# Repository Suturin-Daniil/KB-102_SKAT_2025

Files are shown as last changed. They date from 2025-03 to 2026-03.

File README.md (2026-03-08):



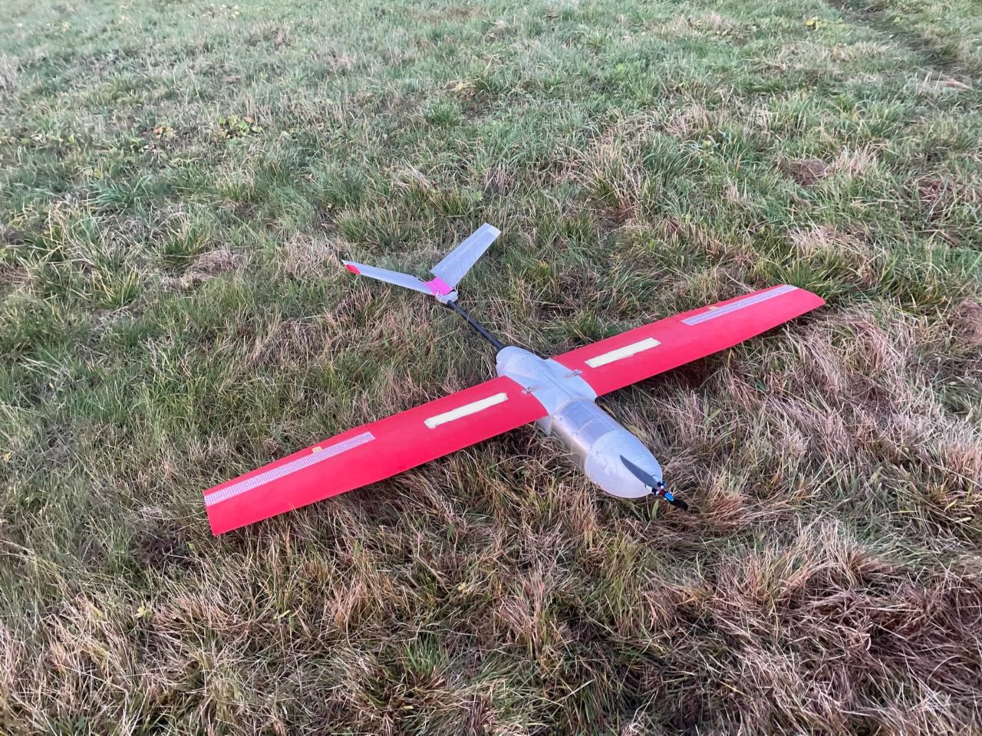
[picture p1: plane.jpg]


# Репозиторий команды КБ-102

В этом репозитории содержится процесс разработки ЛА командой "КБ-102" в рамках студенческого конкурса авиамодельного творчества СКАТ 2025

## Структура репозитория

- **КонцептуальныйДизайн** - папка содержит резльтаты концептуального дизайна ЛА. Описание аэродинамической схемы. Начальная модель ЛА

<!-- - **ПромежуточныйДизайн** - папка промежуточного отчета, содержащая детализированую модель ЛА, начальные аэродинамические и прочностные исследования. Описано бортовое оборудование

- **Изготовление** - папка производственного отчета, содержит конечный вариант детальной модели ЛА, представлены результаты численного моделирования полета ЛА, статической и динамической стабильности. Прочностные расчеты

- **ПолетныйКонтроллер** - содержит электрические схемы полетного контроллера и платы распределения питания собственной разработки. А также динамическую модель ЛА и разрабатываемый автопилот-->

- **Смета** - смета на полетный контроллер и ЛА 

График работ (https://disk.yandex.ru/i/gJ8DDl-IPzN4OA)

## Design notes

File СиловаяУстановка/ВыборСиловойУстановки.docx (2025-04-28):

# 1 Силовая установка

# 1.1 Выбор воздушного винта

Подход к выбору формы и размера пропеллера основан на экспериментальных данных, полученных при испытании воздушных винтов в аэродинамической трубе [1]. Команда выбирала пропеллеры, которые бы давали необходимую тягу для выбранной скорости горизонтального полета с диапазоном частот вращения, который включен в набор угловых скоростей вращения в экспериментальных данных ( 3000÷6000 мин^(-1) ) [1], чтобы быть уверенными в полученных командой оценках. Согласно теории [2 стр. 52], разработанной для оценки тяги и механического момента винта, их выражения имеют следующий вид:

| T= (ρD^4)/(4π^2)Ω^2 C_T | (1)
| Q_p = (ρD^5)/(4π^2)Ω^2 C_Q | (2)

Безразмерные коэффициенты тяги и момента винта могут быть разложены в ряд по степеням поступи винта J= (2πV_a)/(ΩD) (3-4). На рисунке 1 представлены графики зависимости коэффициентов винта от поступи и линии квадратичной аппроксимации.

| C_T =C_(T_0) +C_(T_1) J+C_(T_2) J^2 | (3)
| C_Q =C_(Q_0) +C_(Q_1) J+C_(Q_2) J^2 | (4)

Для оценки потребной тяги при горизонтальном полете со скоростью 18 м/с воспользуемся формулой согласно [3 стр. ]:

| T= W/K= 35/10=3.5 Н | (5)

В ходе анализа различных воздушных винтов, удовлетворяющих требованиям потребной тяги, был выбран винт AeroNaut 11x8

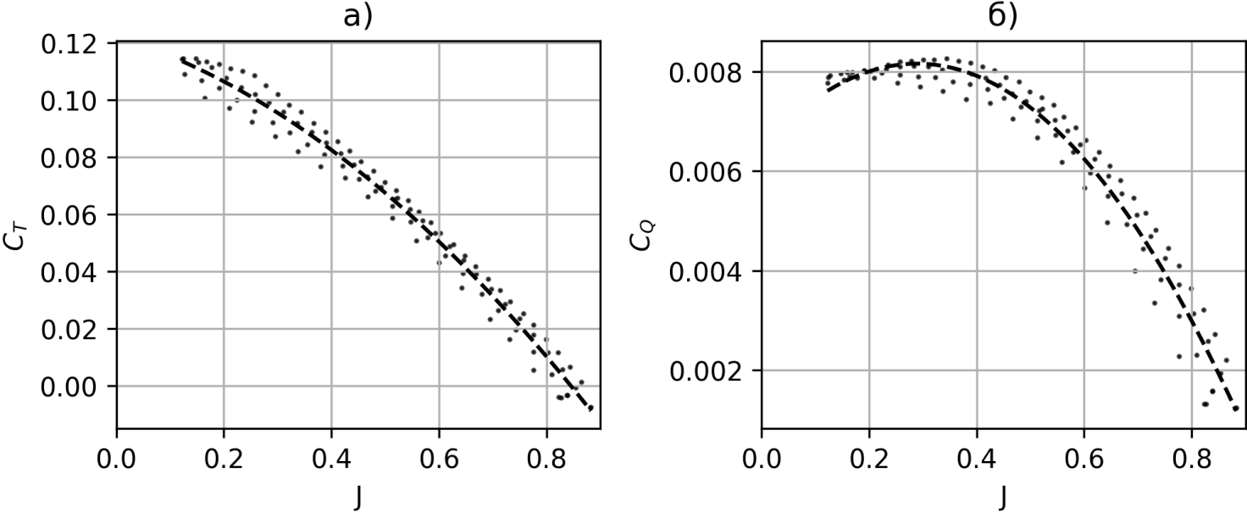
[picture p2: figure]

Рисунок 1 – Коэффициент тяги а) и момента б) винта AeroNaut 11x8

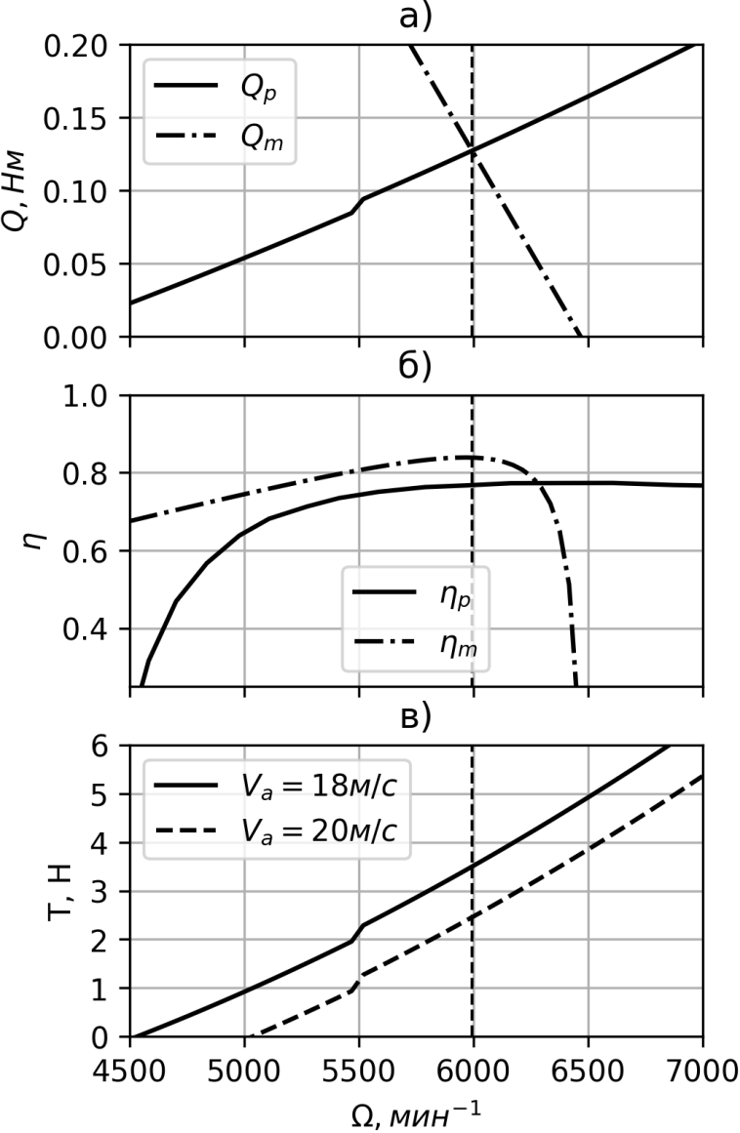
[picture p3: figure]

Рисунок 2 – Выбор оптимальных параметров мотора X2814 и винта AeroNaut 11x8 при горизонтальном полете V_a =18 м/с . а) – пересечение кривых моментов винта и мотора. б) – кривые эффективности мотора и винта. в) – кривые тяги винта. Вертикальная пунктирная линия указывает рабочую частоту вращения

# 1.2 Выбор мотора

В ходе анализа ряда моторов (таблица 1) был выбран Sunnysky X2814 900 kv, так как он оптимален по потребляемой мощности для всех рассматриваемых воздушных винтов. Согласно [2 стр. 53] из равенства механических моментов винта и мотора была найдена точка пересечения кривых моментов винта и мотора (рисунок 2а), соответствующая угловой скорости вращения 6000 мин⁻¹.

Q_m =K_Q (((V_(in) -K_V Ω))/(R-i_0))=Q_p | (6)

Также были построены кривые КПД мотора и винта на рисунке 2б, чтобы убедиться в оптимальном режиме работы ВМГ в выбранном диапазоне угловых частот вращения. Как видно на рисунке 2б, и мотор, и винт на частоте 6000 мин⁻¹ имеет КПД близкий к максимальному для выбранной скорости воздушного полета V_a =18 м/с , η_p = 0.78, η_m =0.84

На рисунке 3в представлены кривые тяги винта в зависимости от частоты вращения для двух разных скоростей воздушного потока. При выбранной скорости 17 м/с винт создает достаточную тягу T=3.5 Н для поддержания установившегося горизонтального полета.

Согласно выражению (6) и рисунку 2а можем оценить мощность, потребляемую ВМГ, с учетом эффективности регулятора оборотов η_(ESC) ≈0.85 :

P=(((Q_m)/(K_V +i_0)))/(η_(ESC))V_(in) ≈110 ВТ | (7)

# 1.3 Оценка энергопотребления

Оценим энергопотребление СУ и БО, согласно расчетам потребления мотора, приведенным выше, и данным о потребляемой мощности для ПК, датчиков, сервоприводов. Ниже в таблице 1 представлены мощности отдельных элементов БО и СУ.

ВМГ | ПК, датчики, связь | Сервоприводы
110 Вт | 7 Вт | 10 Вт

Таблица 1 – энергопотребление элементов бортового оборудования и СУ

Винт Мотор | APC 11x7E¹ (6200 RPM) | APC 11x7S² (5800 RPM) | APC 12x6E¹ (6400 RPM) | AeroNaut 11x8F³ (5800 RPM) | APC 11x8E¹ (5800 RPM) | AeroNaut 12x8F³ (5600 RPM)
T-Motor AT2814 900 kv | 98 Вт | 105 Вт | 105 Вт | 96 Вт | 102 Вт | 107 Вт
T-Motor AT2820 880 kv | 100 Вт | 100 Вт | 101 Вт | 92 Вт | 97 Вт | 101 Вт
T-Motor AT2814 1050 kv | 99 Вт | 99 Вт | 100 Вт | 91 Вт | 96 Вт | 101 Вт
T-Motor AT2820 1050 kv | 101 Вт | 100 Вт | 102 Вт | 93 Вт | 98 Вт | 102 Вт
Sunnysky X2814 900 kv | 96 Вт | 101 Вт | 105 Вт | 94 Вт | 93 Вт | 97 Вт
Sunnysky X2814 1000 kv | 98 Вт | 103 Вт | 106 Вт | 95 Вт | 95 Вт | 99 Вт
Sunnysky X2820 800 kv | 95 Вт | 100 Вт | 103 Вт | 92 Вт | 92 Вт | 96 Вт
Sunnysky X2820 920 kv | 95 Вт | 99 Вт | 103 Вт | 92 Вт | 92 Вт | 96 Вт

Таблица 2 – Энергопотребление моторов при вращении различных воздушных винтов при скорости набегающего потока воздуха 18 м/с и тяге T=3.5 H ¹ Thin Electric, ² Sport, ³ Складной винт

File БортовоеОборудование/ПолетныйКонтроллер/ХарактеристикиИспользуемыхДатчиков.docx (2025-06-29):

Характеристики используемого бортового оборудования и полетного контроллера

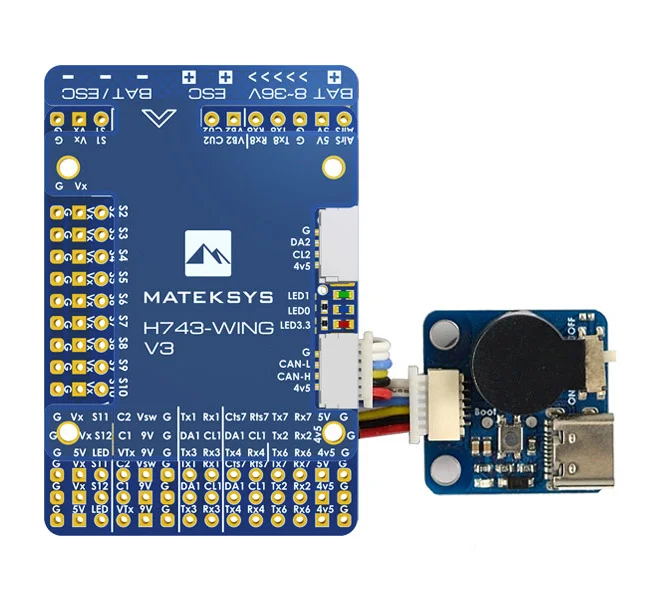
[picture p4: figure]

1. Полётный контроллер MATEKSYS H743-WING V3

Параметр | Значение
Микроконтроллер | STM32H743VIT6 (480 МГц)
Интерфейсы | UART (7) PWM (13) I2C (2) CAN (1)
Прошивка | ArduPilot
Входное напряжение | 8 - 36 В (3-8S LiPo)
Потребляемый ток | 160 мА
Размеры | 54мм × 36мм × 13мм
Вес | 30 г
Стоимость | 13700р (https://mydrone.ru/poletnyy-kontroller-mateksys-h743-wing-v3/)

2. Приемник (телекоманды) Mateksys ELRS 2,4 ГГц

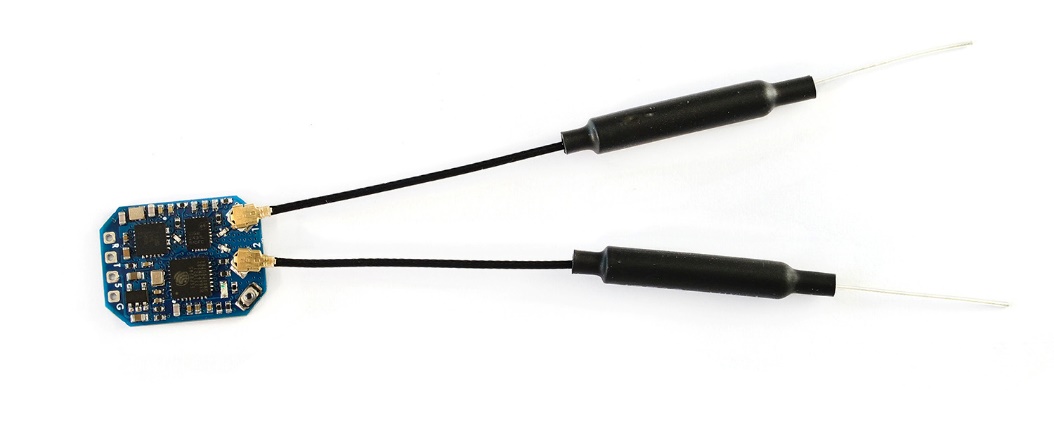
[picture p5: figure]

Параметр | Значение
Антенный разъем | IPEX MHF 1
Рабочая частота | 2,4 ГГц (2400–2480 МГц)
Мощность передачи | 22,5–23 дБм
Коэффициент усиления RX | 12,5 дБ
Протокол приемника | CRSF
Входное напряжение | 4–9 В (контакт 5 В)
Потребляемый ток | 40–45 мА (до привязки) 70–75 мА (привязка)
Размеры | 21мм × 15мм × 5мм
Вес | 3 г
Стоимость | 1800р (https://aliexpress.ru/item/1005006832122747.html?sku_id=12000038446411131)

3. ГНСС и компас Mateksys M10Q-5883

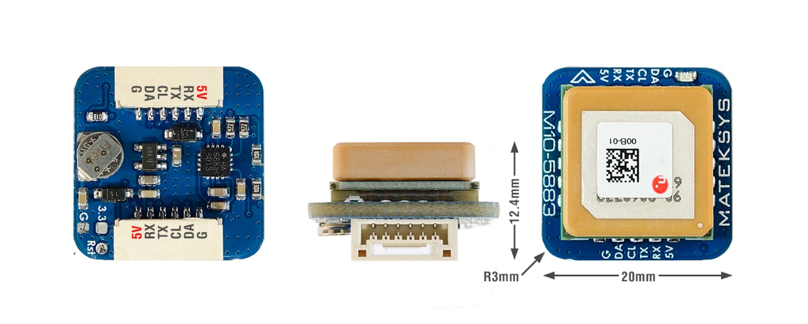
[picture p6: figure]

Параметр | Значение
Патч-антенна | 15 × 15 × 4 мм
Диапазон входного напряжения | 4–9 В (контакт 5 В)
Потребляемый ток | 13 мА
Скорость передачи UART | 9600 (по умолчанию)
Рабочие температуры | -20–80 °C
Интерфейсы | UART (TX, RX) для GNSS I2C (DA, CL) для компаса QMC5883L
Разъем | JST-GH-6P (SM06B-GHS-TB), шаг 1,27 мм
Размеры | 20мм × 20мм × 12,4 мм
Вес | 8 г
Стоимость | 4540р (https://amperkot.ru/msk/catalog/navigatsionnyiy_modul_s_kompasom_mateksys_gnss_m105883-40002749.html)

4. Цифровой датчик воздушной скорости Mateksys ASPD-4525

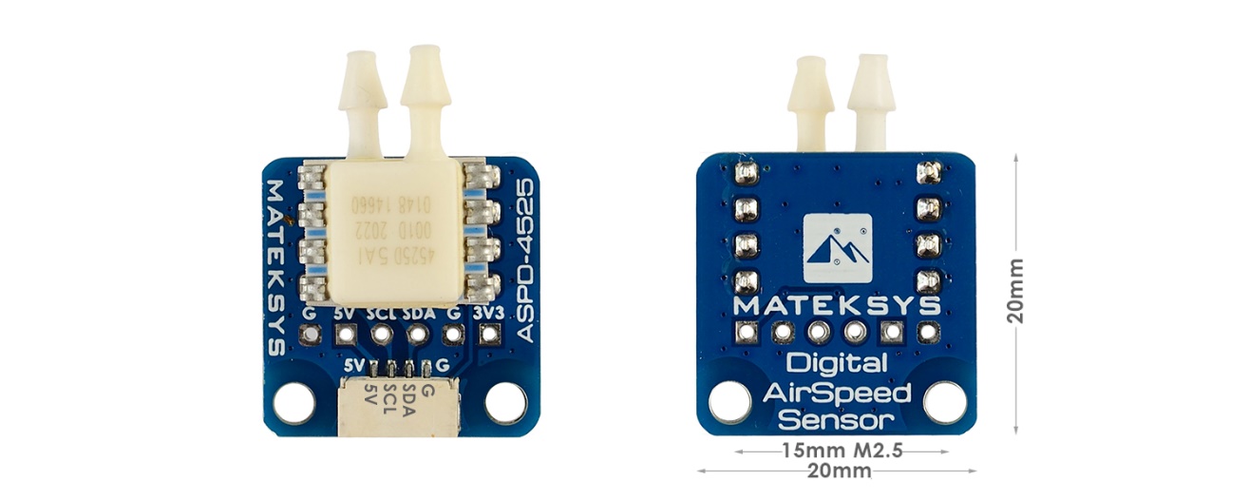
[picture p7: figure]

Параметр | Значение
Напряжение питания платы | 4–5 В
Датчик | TE 4525DO-DS5AI001DP
Потребляемый ток | 5 мА
Интерфейс | I2C (SCL и SDA)
Диапазоны давления | 1 psi (0,069 атм.)
Максимальное давление | 20 psi (1,36 атм.)
Рабочая температура | -40 °C ~ 125 °C
Точность | ±0,25%
Размеры | 20мм × 20мм × 13мм
Вес | 3,5 г (плата)
Стоимость | 6800р (https://mydrone.ru/datchik-skorosti-poleta-mateksys-aspd-4525/)

5. Лидар Mateksys 3901-L0X

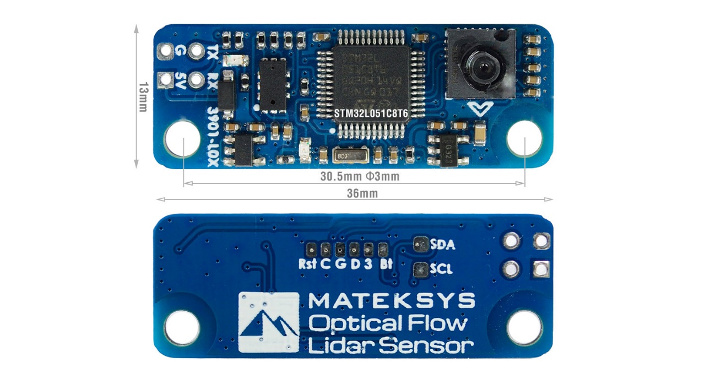
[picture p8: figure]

Параметр | Значение
Напряжение питания платы | 4,5–5,5 В
Датчик | PMW3901
Потребляемый ток | 40 мА
Интерфейс | UART
Рабочий диапазон | 8 см ~ 200 см
Поле зрения | 42°
Размеры | 13мм × 36мм × 6мм
Вес | 2 г
Стоимость | 4100р (https://mydrone.ru/opticheskiy-lazernyy-datchik-mateksys-3901-l0x/)

6. Приемник (телеметрия) Ebyte E32-433T30D

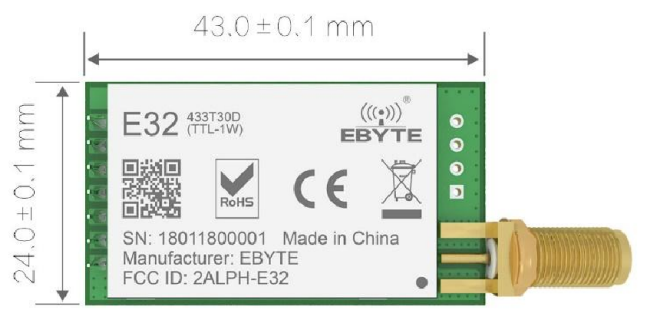
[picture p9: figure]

Параметр | Значение
Антенный разъем | SMA-K
Рабочая частота | 433 МГц (410 – 441 МГц)
Мощность телеметрии | 29,5–30,5 дБм
Дальность связи | 8 км
Протокол приемника | UART
Входное напряжение | 3,3–5,2 В (контакт 5 В)
Потребляемый ток | 610 мА (передача) 20 мА (прием)
Размеры | 24мм × 43мм × 8мм
Вес | 15 г
Стоимость | 1000р (https://aliexpress.ru/item/1005001781692056.html?ysclid=m8vblqdy3n405646056&sku_id=12000042933131057)

7. Мотор DYS Brushless D3548 790 kv

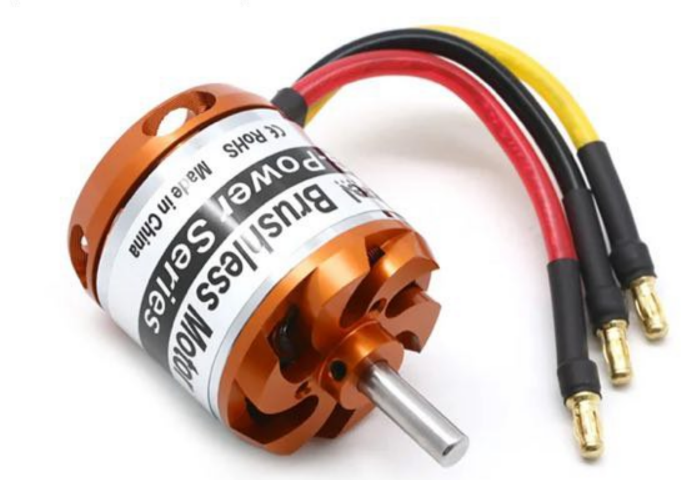
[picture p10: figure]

Параметр | Значение
Напряжение питания платы | 12,2–21 В (3-5s LIPO)
Потребляемый ток | 70 А
Максимальная мощность | 717Вт
Обороты на вольт (kv) | 790
Размеры | 65мм × 35мм × 27,6мм
Вес | 156 г
Стоимость | 2000р (https://aliexpress.ru/item/32951513519.html?ysclid=m9ff9l9cy8213148519&sku_id=12000030265700724)

8. Hobbywing Skywalker ESC 80A UBEC

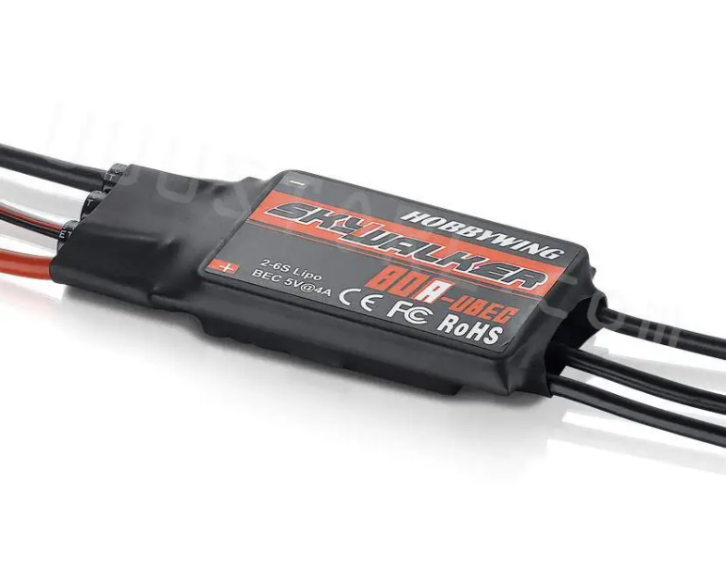
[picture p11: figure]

Параметр | Значение
Входное напряжение | 2-6 S Lipo
Выходной ток | 80А (макс. 100А на 10 сек)
Размеры | 86 мм × 38 мм × 12 мм.
Вес | 82 г
Стоимость | 2000р (https://aliexpress.ru/item/32725855320.html?ysclid=m9ejq9qvl3565869684&sku_id=12000024799959275)

9. Rush Solo Tank 5,8G VTX видеопередатчик

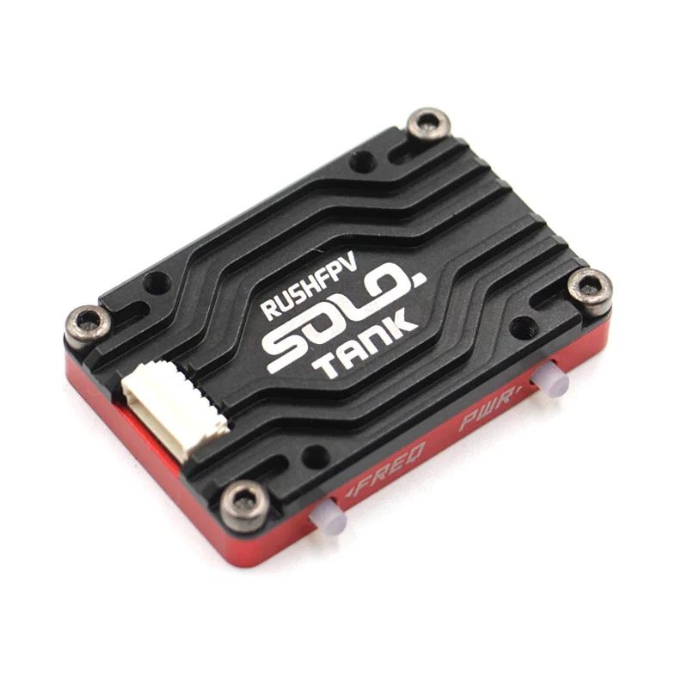
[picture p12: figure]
Picture background

Параметр | Значение
Антенный разъем | MMCX
Рабочая частота | 5,8 ГГц
Мощность передатчика | 25/400/800/1600 мВт
Формат видео | CVBSPAL / NTSC
Входное напряжение | 7 - 36 В
Размеры | 37мм × 24мм × 6,7мм
Вес | 12 г
Стоимость | 8000р (https://mydrone.ru/videoperedatchik-rush-tank-solo/?ysclid=m9ekt82tw6376214830)

10. Сервопривод PDI-HV2006MG CORELESS

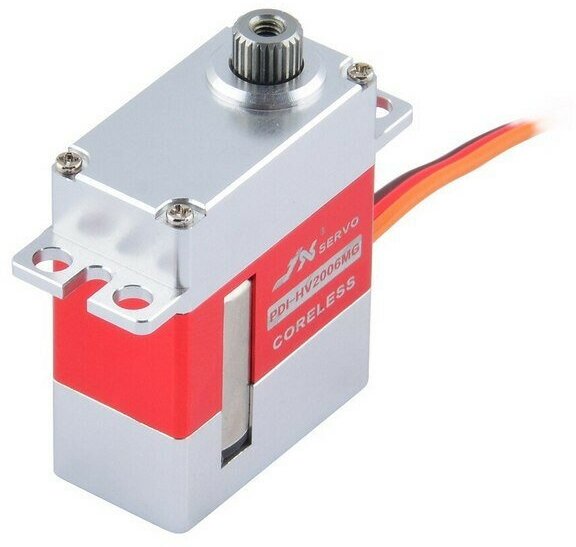
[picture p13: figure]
Picture background

Параметр | Значение
Напряжение питания платы | 6–8,4 В
Потребляемый ток | 1350 мА
Управление | ШИМ
Момент | 6.2кг.см (7,4В) – 4,8кг.см (6В)
Скорость | 0,05 сек /60° (7,4В) – 0,07 сек / 60° (6В)
Рабочие температуры | -10–60 °C
Размеры | 23мм × 12мм × 27,6мм
Вес | 20 г
Стоимость | 2000р (https://aliexpress.ru/item/1005004446353107.html?ysclid=m9fdrbq94s201175639&sku_id=12000029206493623)

11. FPV Камера Foxeer Mini Predator 5

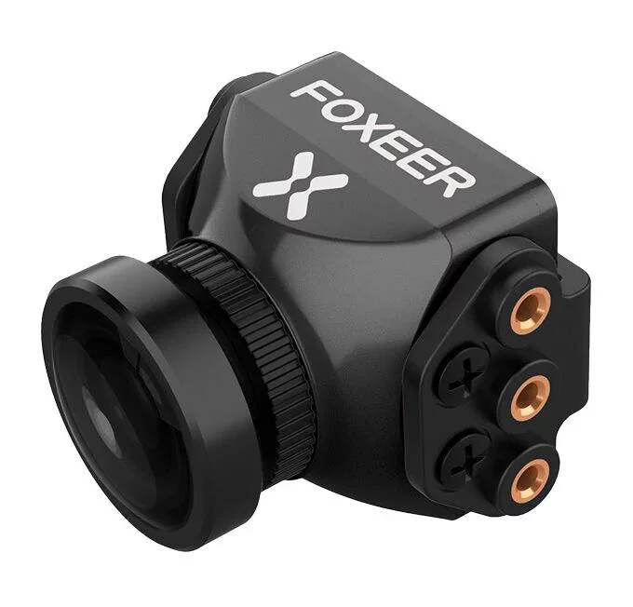
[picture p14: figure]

Параметр | Значение
Напряжение питания платы | 4,5 - 20 В
Потребляемый ток | 50 мА ± 15% (12 В)
Линза | 1,8мм
Матрица | Sony 1/3" CMOS-сенсор
Угол обзора | 115°(горизонталь), 150°(диагональ)
Рабочие температуры | -10–50 °C
Размеры | 28мм × 22мм × 30мм
Вес | 12 г
Стоимость | 5000р (https://mydrone.ru/fpv-kamera-foxeer-mini-predator-5-chernyy-1.8-linza/)

Тип БО | Степень критичности | Последствия | Действия команды
Полетный контроллер | Критично | Неконтролируемое падение | Отход от позиций возможного падения
Регулятор оборотов, мотор | Критично | Отсутствие тяги | Переход на ручное управление и обеспечение плавного спуска БВС за счет управляющих поверхностей
Сервоприводы | Критично | Отсутствие маневренности | Переход на ручное управление и обеспечение плавного спуска БВС за счет мотора
Радиоприемник телекоманд | Критично | Отсутствие связи с БВС | Возвращение БВС на точку старта в автоматическом режиме
Радиопередатчик телеметрии | Средняя степень критичности | Отсутствие данных о состоянии БВС | Сохранение телеметрии на память БВС
Камера FPV, передатчик видео потока | Средняя степень критичности | Отсутствие видео потока | Визуальное сопровождение
Датчик воздушной скорости | Средняя степень критичности | Отсутствие данных о скорости потока | Переход на ручное управление
GPS, компас | Средняя степень критичности | Отсутствие данных положения БВС | Переход на ручное управление

Таблица 1. степени критичности выхода из строя того или иного элемента бортового оборудования. Последствия выхода из строя подсистемы, действия команды в случае отказа той или иной подсистемы

Вероятность отказа всех систем уменьшается за счет использования надежных способов коммутации (пайка и клеммы) датчиков и управляющих элементов с полетным контроллеров, а также за счет обеспечения стабильного питания от аккумуляторных батарей.

Характеристика | Значение
Потребляемая мощность | 136 Вт
Масса | 450 г
Цена | 57 тыс. руб.

Таблица 2. Суммарные значения массы, потребляемой мощности, цены бортового оборудования

Тип БО | Название | Интерфейс | Вес | Размеры
Полетный контроллер | MATEKSYS H743-WING V3 | UART (7) PWM (13) I2C (2) CAN (1) | 30 г | 54мм × 36мм × 13мм
Радио модуль (телеметрия) | Ebyte E32-433T30D | UART | 15 г | 24мм × 43мм × 8мм
Радио модуль (телекоманды) | Mateksys ELRS 2,4 ГГц | I2C | 3 г | 21мм × 15мм × 5мм
Радио модуль (Видео) | Rush Solo Tank 5,8G VTX | – | 12 г | 37мм × 24мм × 6,7мм
Навигационный модуль | Mateksys M10Q-5883 | UART для GNSS I2C для компаса | 8 г | 20мм × 20мм × 12,4 мм
FPV камера | Foxeer Mini Predator 5 | – | 12 г | 28мм × 22мм × 30мм
Регулятор оборотов | Hobbywing Skywalker ESC 80A UBEC | – | 82 г | 86 мм × 38 мм × 12 мм
Сервопривод | PDI-HV2006MG CORELESS | ШИМ | 20 г | 23мм × 12мм × 27,6мм

Таблица 3 – используемое БО

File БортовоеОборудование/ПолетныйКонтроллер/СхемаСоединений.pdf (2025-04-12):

## motor

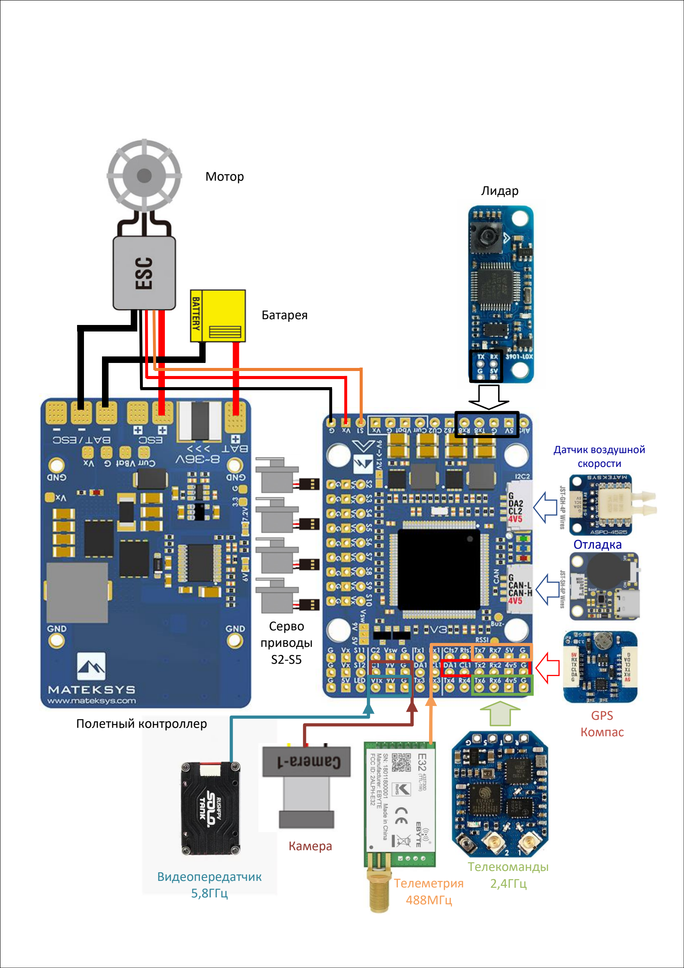
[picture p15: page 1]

S2-S5
servos

Телеметрия
488МГц

Телекоманды
2,4ГГц

GPS
Компас

Отладка

Датчик воздушной
скорости

Лидар

Серво
приводы
S2-S5

Мотор

Полетный контроллер

Видеопередатчик
5,8ГГц

Камера

Батарея

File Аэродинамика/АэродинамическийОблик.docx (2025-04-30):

## Проектный отчет команды «КБ-102»

# 1 Список сокращений и обозначений

α-угол атаки ЛА | V_a -скорость ЛА относительно воздушного потока | δ_e -угол отклонения управляющих поверхностей
C_l -коэффициент подъемной силы профиля | S_(w,t) -площадь крыла, хвостового оперения | C_(L_i ,D_i ,M_i) -производная аэродинамического коэффциента по параметру i
C_L -коэффициент подъемной силы ЛА | b-размах | λ-сужение
C_D -коэффициент силы лобового сопротивления ЛА | с-средняя аэродинамическая хорда | с_r -корневая хорда крыла
W-вес ЛА | i_w -угол установки крыла | A-удлинение

Команда использует обозначения согласно ISO 1151, чтобы иметь соответствие с обозначениями принятыми в модели динамики ЛА, разрабатываемой командой.

# 2 Аэродинамический облик

В ходе проектирования аэродинамического облика ЛА команда использовала инженерные методы оценки на основе экспериментальных данных, приведенных в [1, 2, 3]. Не смотря на то, что в источнике [1] числа Рейнольдса, при которых проводились эксперимент, выше, чем те, при которых будет эксплуатироваться разрабатываемый ЛА; приводимые оценки отражают динамику изменения аэродинамических характеристик ЛА. Был написан Python код, включающий в себя все выражения и взаимосвязи, описанные в данном разделе. Это позволило быстро оценивать аэродинамические характеристики ЛА по изменению входных данных: геометрия ЛА, масса, типы аэродинамических профилей и т.д.

После того, как аэродинамический облик был сформирован, были использованы методы численного моделирования для уточнения параметров и приведения их в соответствие с требуемыми значениями для выполнения ТЗ.

# Фюзеляж

Выбор формы фюзеляжа и его геометрических размеров (рисунок 1) основан на оценке места, занимаемого БО и грузом; а также на простоте в построении геометрии и в дальнейшем изготовлении. Для размещения необходимых элементов был выбран круговой профиль в поперечном сечении фюзеляжа, что также обеспечивает лучшие аэродинамические характеристики по сравнению с прямоугольным при таком же миделевом сечении. Длина фюзеляжа составила 1300 мм

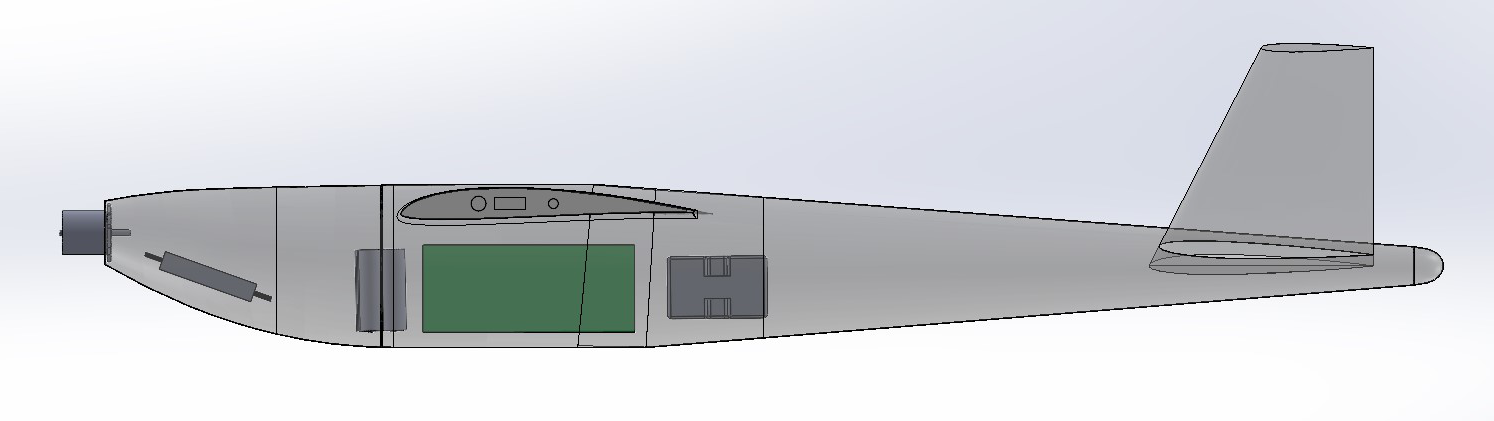
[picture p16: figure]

Рисунок 1 – Общий вид ЛА

# Аэродинамические профили

На основе оценок атласа низкоскоростных профилей [4] был выбран SD7032 для крыла, обладающий приемлемыми характеристиками: спроектирован для эксплуатации на низких числах Рейнольдса (300 000), имеет плавную зависимость C_l (α) на закритическом режиме, высокое аэродинамическое качество.

Особенностью симметричных профилей на низких скоростях является нелинейный характер зависимости коэффициента подъемной силы от угла атаки вблизи α=0° [4, стр. 40]. Однако анализ ряда профилей показал в ходе исследования статической устойчивости, что нелинейности не оказывают существенного влияния на способность ЛА удерживать заданный угол атаки в широком диапазоне. Для хвостового оперения был выбран симметричный NACA0008.

# Геометрические характеристики крыла

Начальная оценка потребной площади крыла и его геометрических характеристик основывалась на предположении, что крыло должно создавать необходимую подъемную силу для компенсирования веса ЛА при заданной скорости горизонтального полета V_a =18 м/с , так как геометрические характеристики хвостового оперения и фюзеляжа и их вклад в C_L и C_D еще не определен. Тогда оценка для площади крыла имеет вид:

| S= (2W)/(ρV_a^2 C_L)= (2⋅35)/(1.225⋅18^2 ⋅0.5)=0.352 м^2 | (1)

Где C_L был выбран равным 0.5, как целевой коэффициент подъемной силы в горизонтальном полете, который будет в дальнейшем уточнен и оценен из характеристик построенной геометрии ЛА.

Скорость сваливания является важным показателем для оценки потребной площади крыла, его геометрических характеристик и размеров управляющих поверхностей, так как они влияют на достижимый максимальный коэффициент подъемной силы всего ЛА C_(L_(max)) , определяющий значение скорости сваливания. Для оценки скорости, сообщаемой человеком при запуске с рук V_0 , был проведен эксперимент, в ходе которого на скоростную съемку был записан момент броска объекта массой 3.5 кг. Из анализа видеозаписи была вычислена V_0 :

| V_0 = 7-8 м/c | (2)

Геометрические характеристики крыла представлены в таблице 1:

A | λ, м | b, м | c, м | c_r , м | S, м^2 | i_w , °
8 | 0.750 | 1.678 | 0.210 | 0.236 | 0.352 | 1.8

Таблица 1 – Геометрические характеристики крыла

# Хвостовое оперение

Для оценки площади хвостового оперения (ХО) воспользуемся методом объёмных коэффициентов ([1] стр. 158-161). В нашем случае ХО имеет V-образный тип, поэтому под горизонтальным (HT) и вертикальным (VT) ХО будем понимать проекции ХО на горизонтальную и вертикальную плоскости соответственно.

Согласно ([1], стр. 160) примем объёмные коэффициенты вертикального и горизонтального оперений c_(HT) =0.6, c_(VT) =0.04 . Возьмём плечо момента рыскания, создаваемого вертикальным оперением L_(VT) равным плечу момента тангажа, создаваемого горизонтальным оперением L_(HT) и равным L≈0.8м . Тогда площади вертикального и горизонтального оперений равны

| S_(VT) =(c_(VT) bS)/(L_(VT))≈0.029м^2 , S_(HT) =(c_(HT) cS)/(L_(HT))≈0.055м^2 | (3)

Их сумма даёт полную площадь хвостового оперения S_T =S_(HT) +S_(VT) ≈0.085м^2 . Угол наклона одной лопатки относительно горизонтальной плоскости Γ=arctg((S_(VT))/(S_(HT)))≈28^o , тогда угол раствора лопаток. Геометрические характеристики ХО представлены в таблице 2

S_t , м^2 | λ_t | A_t | b_t , м | c, м | c_r^t , м | Γ, °
0.085 | 0.6 | 2 | 0.291 | 0.146 | 0.182 | 28

Таблица 2 – Геометрические характеристики хвостового оперения

# Управляющие поверхности

Размер управляющих поверхностей и доля размаха хвостового оперения и крыла, занимаемого ими, указаны в таблице 3.

| Элероны | Руль высоты
Доля хорды ( c_f /c ) | 0.3 | 0.3
Доля размаха ( b_f /b ) | 0.5 | 0.8

Таблица 3 – Характеристики управляющих поверхностей

Выбор такой геометрии обусловлен тем, что предельная эффективность управляющих поверхностей (максимальный прирост ΔC_L за счет отклонения рулей) (рисунок 2) достигается при небольших углах отклонения рулей до 20°÷25° . Более того, как будет показано далее, такая конфигурация обеспечивает статическую устойчивость в продольном канале ЛА.

# Модель коэффициента подъемной силы

Для оценки C_L всего ЛА была рассмотрена модель коэффициента подъемной силы согласно источнику [5]:

| C_L (α, δ_e , q)=C_(L_0) +C_(L_α) α+C_(L_(δ_e)) δ_e +C_(L_q) c/(2V_a)q | (4)

Последовательно оценим вклад крыла и хвостового оперения в каждое слагаемое в (4), кроме последнего, так как в данном отчете рассматривается лишь стационарный полет ЛА, подразумевающий p=q=r=0 .

Второе слагаемое состоит из вклада хвостового оперения и крыла при δ_e =0 . Согласно [1] C_(L_α) можно оценить следующим образом, учитывая геометрию крыла:

| C_(L_α) = (2πA)/(2+ √((A^2 β^2)/(k^2 (α))(1+ (tg^2 (Λ_(c/2) ))/(β^2))+4)) | (5)

Таким образом, второе слагаемое в (4) имеет вид:

| C_(L_α) (α)α≈C_(L_α) α=(C_(L_α)^w +(S_(ht))/SC_(L_α)^t )α=(4.71+ 0.053/0.3522.87)α= 5.14α | (6)

Первое слагаемое в (4) вновь включает вклад крыла и хвостового оперения. Для оценки значения C_(L_0) воспользуемся методом, описанным в [2], предполагающий отсутствие изменения в угле атаки α_0 , при котором C_l (α_0 )=C_L _0 (α_0 )=0 .

| C_(l_0) =-α_0 C_(l_α) , α_0 = -(C_(l_0))/(C_(l_α)) | (7)

| C_(L_0) =|α_0 |C_(L_a) = |(C_(l_0))/(C_(l_α))|C_(L_a) | (8)

С учетом полученного выражения (8) получим первое слагаемое из (4), которое имеет вид:

| C_(L_0) =С_(L_0)^w + (S_(ht))/SC_(L_0)^t =0.498+ 0.053/0.3520.0=0.498 | (9)

Наконец оценим вклад третьего слагаемого в (4). Для его определения был использован метод, представленный в [1], предполагающий оценку влияния отклонения управляющих поверхностей на C_l для крыла бесконечного размаха фиксированного профиля (10), а затем учет геометрических характеристик крыла для вычисления приращения коэффициента подъемной силы ΔC_L за счет отклонения рулевых поверхностей (11).

| ΔC_l =δ((C_(l_δ))/((C_(l_δ) )_(теор)))(C_(l_δ) )_(теор) K^(') | (10)

| ΔC_L =ΔC_l ((C_(L_α))/(C_(l_α)))mK_b = δ((C_(l_δ))/((C_(l_δ) )_(теор)))(C_(l_δ) )_(теор) K^(') ((C_(L_α))/(C_(l_α)))mK_b | (11)

где K^(') и K_b – экспериментальные поправочные коэффициенты для эффективности подъемной силы за счет отклонения управляющих поверхностей и доли площади крыла, занимаемой управляющими поверхностями, соответственно. На рисунке 2 изображен вклад хвостового оперения и крыла в C_L при отклонении управляющих поверхностей согласно выражению (11). Приведем также численное значение третьего слагаемого в выражении (4) за счет отклонения управляющих поверхностей хвостового оперения в области углов отклонения δ_e = -15°÷15° , где зависимость линейна (рисунок 2)

| C_(L_(δ_e)) δ_e =0.08δ_e | (12)

Отметим, что на рисунке 3 кривая для крыла была построена в предположении совместного отклонения элеронов, например при старте с рук, когда есть возможность их совместного отклонения для увеличения подъемной силы крыла. В горизонтальном полете, когда функция элеронов – управлять креном, представленная зависимость не применима. Однако зависимость может быть обобщена для закрылков, если таковые появятся в конструкции в последующем.

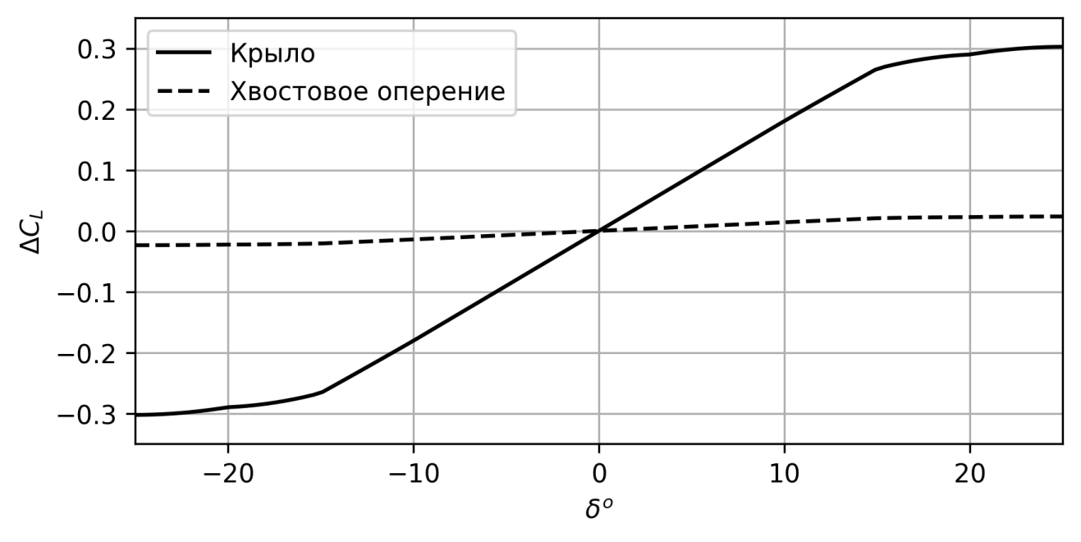
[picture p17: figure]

Рисунок 2 – Приращение коэффициента подъемной силы ЛА за счет отклонения управляющих поверхностей крыла и хвостового оперения

Приведем окончательный вид зависимость коэффициента подъемной силы всего ЛА в случае стационарного полета:

| C_L (α, δ_e )=0.498+5.14α+0.08δ_e | (13)

# Модель коэффициента силы лобового сопротивления

Необходимость в оценке силы сопротивления, действующей на ЛА, обусловлена ее необходимостью для определения подходящей силовой установки и дальнейшего выбора системы питания и оценки продолжительности полета.

Согласно источнику [5] модель коэффициента лобового сопротивления ЛА имеет вид:

| C_D (α, δ_e , q)=C_(D_0) +C_(D_α) α+C_(D_(δ_e)) δ_e +C_(D_q) c/(2V_a)q | (14)

Коэффициент силы лобового сопротивления за счет сил трения C_(D_0) согласно [2] можно оценить, как сумму коэффициентов сил трения элементов конструкции ЛА.

| C_(D_0) =(C_(D_(add)) + 1/S∑_i C_(f_i) ⋅FF_i ⋅S_(wet_i) ⋅IF_i )k_(кэнс) | (15)

где C_f – коэффициент сил трения, FF – множитель, учитывающий форму обтекаемого тела, IF – множитель, учитывающий взаимное расположение и влияние элементов конструкции друг на друга, S_(wet) – полная площадь поверхности элемента, подверженная обтеканию воздушным потоком, C_(D_(add)) - дополнительный коэффициент сопротивления за счет элементов конструкции, не являющихся крылом или фюзеляжем, например, подвесных конструкций на крыле, k_(кэнс) – множитель кумулятивного эффекта нежелательного сопротивления, учитывающий неидеальность конструкции и отличие расчетных форм от действительных

Согласно выражению (15) был проведен подсчет вклада фюзеляжа, крыла и хвостового оперения в C_(D_0) . Для оценки C_f каждого компонента была использована модель турбулентно-ламинарного обтекания тела [2], имеющая следующий вид:

| (x_0)/l=36.9((x_(tr))/l)^0.625 (1/(Re))^0.375 | (16)

| C_f = 0.074/(Re^0.2)(1-((x_(tr) -x_0)/l))^0.8 | (17)

где x_0 – приведенная точка перехода от ламинарного к турбулентному обтеканию тела, x_(tr) – точка перехода от ламинарного к турбулентному режиму обтеканию тела. И x_0 и x_(tr) отсчитываются от передних кромок обтекаемых потоком тел. l – характерная длина обтекаемого тела (хорда крыла, длина фюзеляжа)

Для профиля крыла и хвостового оперения значения x_(tr) были взяты из результатов их анализа в программе XFOIL при Re=300 000 . Для фюзеляжа было принято для всех углов атаки (x_(tr))/l=0.05

| C_(D_0) (Re=300 000)= 0.024 | (18)

Параметр k_(кэнс) согласно [2] имеет значение 1.25 . Результат подсчета вклада первых двух слагаемых в (14) представлен в виде столбчатой диаграммы на рисунке 3.

Для более точной оценки лобового сопротивления в зависимости от угла атаки и геометрических характеристик ЛА используем дополненную квадратичную модель коэффициента лобового сопротивления. Второе слагаемое в (14) заменим следующим образом:

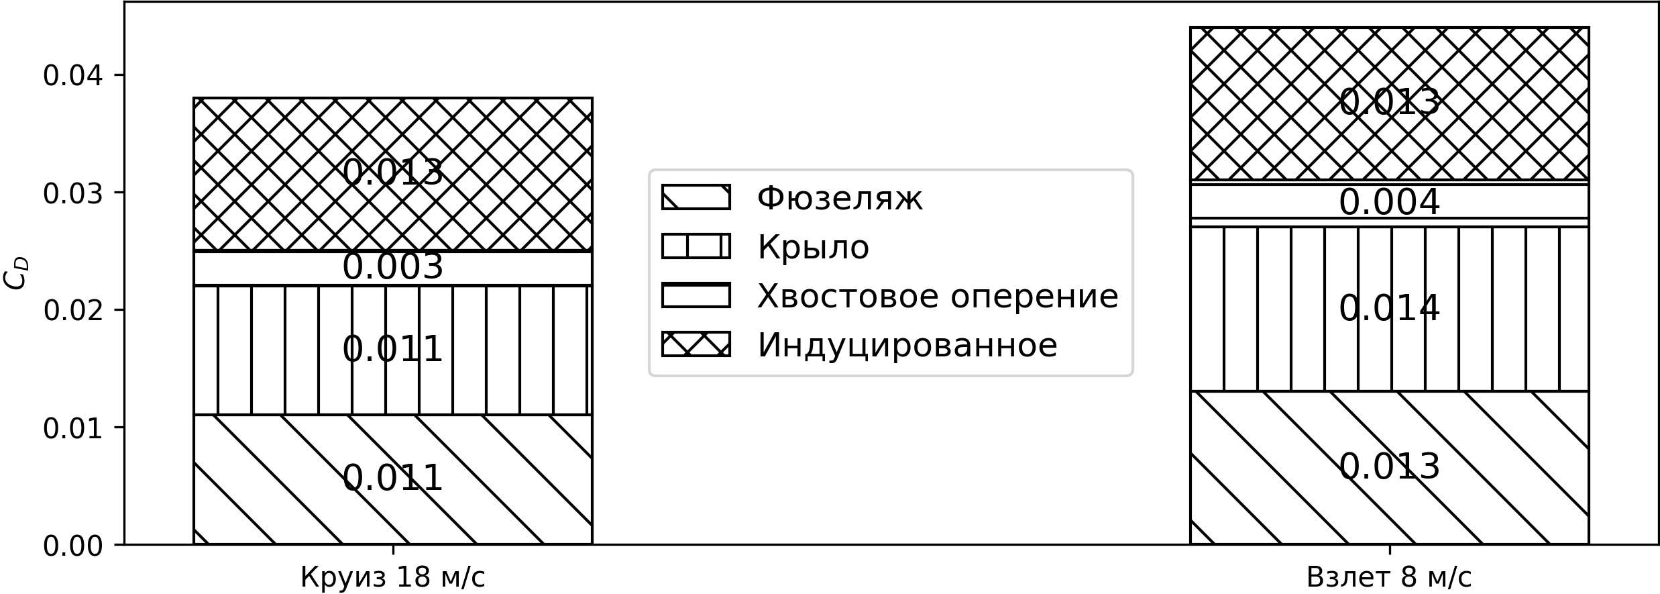
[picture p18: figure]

Рисунок 3 – Покомпонентный вклад в коэффициент лобового сопротивления элементов конструкции и индуцированное сопротивление в горизонтальном полете и при взлете

| C_(D_α) α=C_(D_i) (α)= ((C_L (α)-C_(LminD) )^2)/(πeA) | (19)

Коэффициент эффективности Освальда был оценен согласно выражению из [2]:

| e= 1/(π⋅A⋅r⋅C_(D_0) +1/(((1+0.03t-2t^2 )u)))=0.78 | (20)

где u=0.98 , r=0.38- (Λ_0)/3000+ (Λ_0^2)/15000

| C_(D_α) =(∂C_(D_i))/(∂α)=2/(πeA)(C_(L_0) +C_(L_α) α-C_(LminD) )C_(L_α) =10.28/19.6(0.5+5.14α-0.5)=2.7α | (21)

Так же приведем зависимость индуцированного и сопротивления трения от воздушной скорости (рисунок 4). По нему определим оптимальную скорость горизонтального полета с наименьшей силой лобового сопротивления.

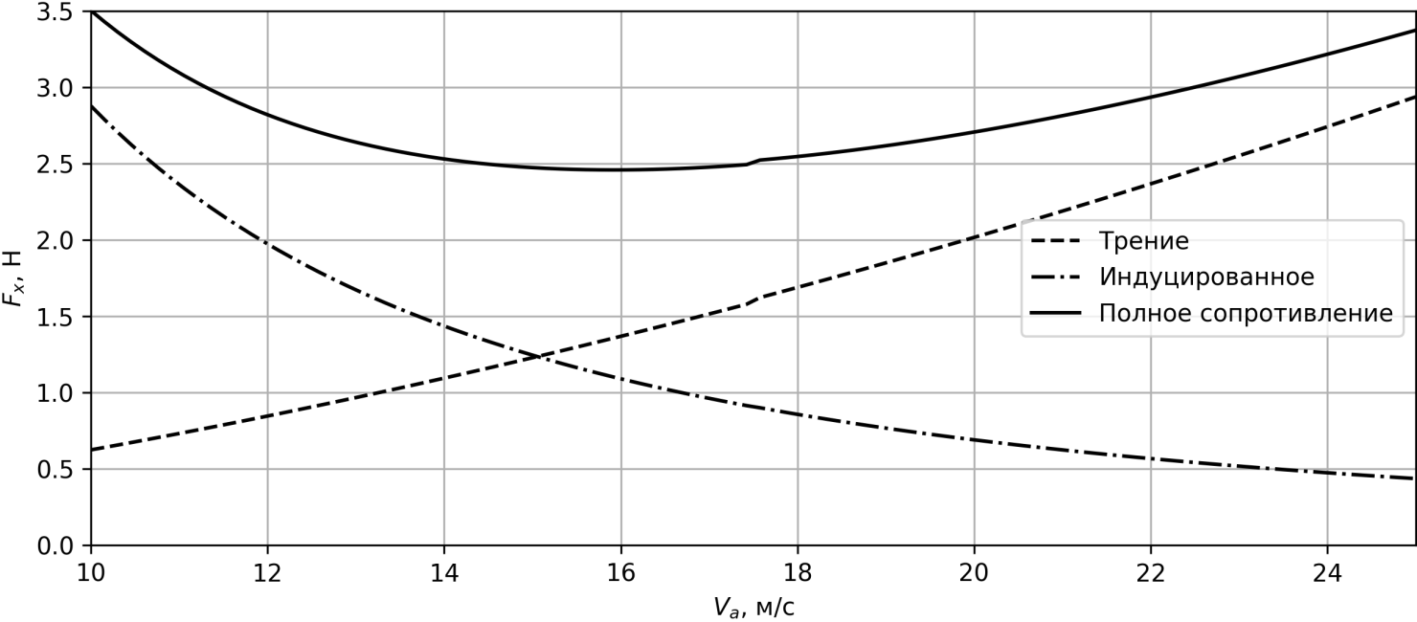
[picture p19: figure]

Рисунок 4 – Зависимость сопротивления трения и индуцированного от воздушной скорости в горизонтальном полете

Видим, что оптимальная скорость полета, обеспечивающая наибольшее время полета равна 16 м/с . Однако для преодоления маршрута длиной 20 км за оценочное время 20 минут была выбрана скорость горизонтального полета 18 м/c

В качестве оценки третьего слагаемого в (14) примем оценку C_(D_(δ_e)) =0.006 согласно [2]. Тогда окончательное выражение для коэффициента лобового сопротивления имеет вид

| C_D (α, δ_e )=0.024+2.7α^2 +0.006δ_e | (22)

# Модель коэффициента момента тангажа

Рассмотрим модель момента тангажа следующего вида:

| C_M =C_(M_0) +C_(M_α) α+C_(M_(δ_e)) δ_e | (23)

Вновь последовательно оценим вклад СУ, крыла и хвостового оперения в три слагаемых выше. Первое слагаемое есть сумма вида: C_(M_0) =C_(M_0)^w +C_(M_0)^t +C_(M_0)^(prop) . Согласно [3] имеем:

| C_(M_0)^w = C_(m_0)^w ((Acos^2 Λ_(c/4))/(A+2cosΛ_(c/4))) + C_(L_0)^w ((l_(cg)^w)/c)= 0.002 | (24)
| C_(M_0)^t =(C_(m_0)^t ((Acos^2 Λ_(c/4))/(A+2cosΛ_(c/4)))((c_(tail))/c)+C_(L_0)^t ((l_(cg)^t)/c))((S_(ht))/S)= 0 | (25)

C_(M_0)^t =0 , так как профиль симметричный и угол установки хвостового оперения равен 0. Вклад СУ с учетом расположения линии тяги выше центра масс имеет вид

| C_(M_0)^(prop) = (2r_m ×T)/(ρV_a^2 Sc)= -(2z_m T)/(ρV_a^2 Sc)= -(2⋅0.03⋅2.6)/(1.225⋅18^2 ⋅0.352⋅0.21)= -0.005 | (26)

Для второго слагаемого в (23) c учетом отклонения крылом набегающего потока и ослаблением его (∂ϵ)/(∂α)=0.1, η=0.9 запишем:

| C_(M_α) = C_(M_α)^w +C_(M_α)^t =C_(L_α)^w ((l_(cg)^w)/c)-η ((S_(ht))/S)C_(L_0)^t ((l_(cg)^t)/c)(1- (∂ϵ)/(∂α))=-0.561 | (27)

Наконец оценим третье слагаемое в (23):

| C_(M_(δ_e)) = -ηC_(L_(δ_e)) ((S_(ht))/S)((l_(cg)^t)/c)= -0.456 | (28)

Приведем окончательный вид зависимости модели коэффициента момента тангажа:

| C_(M_(δ_e)) = -0.003-0.561α-0.456δ_e | (29)

# Статическая устойчивость ЛА в продольном канале

Для анализа ЛА на статическую устойчивость в продольном канале в зависимости от центровки и геометрических характеристик было вычислено положение центра давления и схематически нанесено на рисунке 5. Было найдено оптимальное положение центра масс ЛА, при котором возможен установившийся горизонтальный полет без отклоненных рулей хвостового оперения при массе ЛА 3.5 кг. На основе модели коэффициента момента тангажа (29), которая была получена для оптимального положения центра масс на расстоянии от передней кромки крыла x_(cg) =0.4c , были построены балансировочные кривые (рисунок 6). Балансировочные кривые имеют отрицательный наклон, что говорит о статической устойчивости ЛА в продольном канале

Рисунок 5 – Схематичное положение ЦМ – центра масс, ЦД – центра давления и АЦ – аэродинамического центра крыла

Однако из-за нелинейности прироста как коэффициента подъемной силы, так и момента тангажа за счет отклонения управляющих поверхностей стоит увеличить |C_(M_α) | для большей статической устойчивости согласно (27) путем увеличения размеров хвостового оперения, длины плеча хвостового оперения или же передней центровкой ЛА.

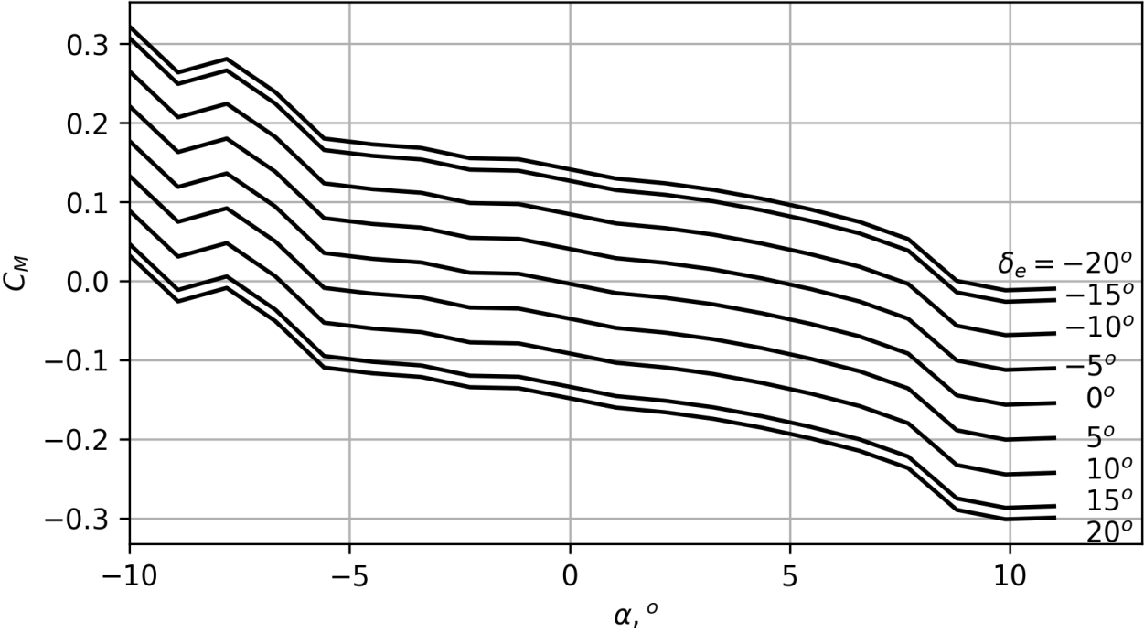
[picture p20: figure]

Рисунок 6 – Балансировочные кривые для координаты центра масс x_(cg) =0.4c

# 3 Силовая установка

# Выбор воздушного винта

Подход к выбору формы и размера пропеллера основан на экспериментальных данных, полученных при испытании воздушных винтов в аэродинамической трубе [6]. Команда выбирала пропеллеры, которые бы давали необходимую тягу для выбранной скорости горизонтального полета с диапазоном частот вращения, который включен в набор угловых скоростей вращения в экспериментальных данных ( 3000÷6000 мин^(-1) ) [6], чтобы быть уверенными в полученных командой оценках. Согласно теории [5 стр. 52], разработанной для оценки тяги и механического момента винта, их выражения имеют следующий вид:

| T= (ρD^4)/(4π^2)Ω^2 C_T | (30)
| Q_p = (ρD^5)/(4π^2)Ω^2 C_Q | (31)

Безразмерные коэффициенты тяги и момента винта могут быть разложены в ряд по степеням поступи винта J= (2πV_a)/(ΩD) (32-33). Согласно рисунку 4 требуемая тяга для поддержания горизонтального полета T=2.5÷3 Н . В ходе анализа различных воздушных винтов, удовлетворяющих требованиям потребной тяги, был выбран винт AeroNaut 11x8.

| C_T =C_(T_0) +C_(T_1) J+C_(T_2) J^2 | (32)
| C_Q =C_(Q_0) +C_(Q_1) J+C_(Q_2) J^2 | (33)

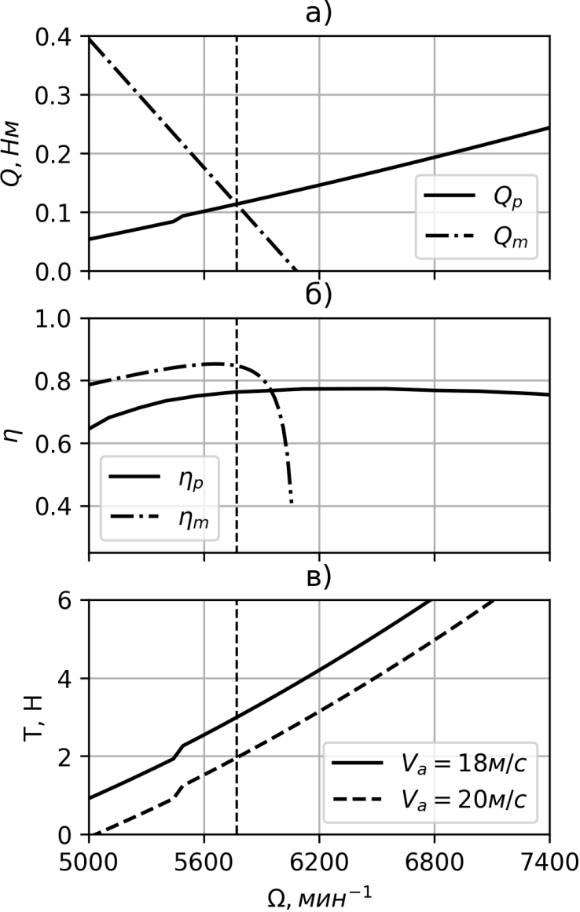
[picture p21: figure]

Рисунок 7 - Выбор оптимальных параметров мотора X2814 и винта AeroNaut 11x8 при горизонтальном полете V_a =18 м/с . а) – пересечение кривых моментов винта и мотора. б) – кривые эффективности мотора и винта. в) – кривые тяги винта. Вертикальная пунктирная линия указывает рабочую частоту вращения

# 3.1 Выбор мотора

В ходе анализа ряда моторов был выбран Sunnysky X2814 900 kv, так как он оптимален по потребляемой мощности для всех рассматриваемых воздушных винтов. Согласно [5 стр. 53] из равенства механических моментов винта и мотора была найдена точка пересечения кривых моментов винта и мотора (рисунок 8а), соответствующая угловой скорости вращения 5800 мин⁻¹.

Q_m =K_Q (((V_(in) -K_V Ω))/(R-i_0)) | (34)

Также были построены кривые КПД мотора и винта на рисунке 8б, чтобы убедиться в оптимальном режиме работы ВМГ в выбранном диапазоне угловых частот вращения. Как видно на рисунке 8б, и мотор, и винт на частоте 5800 мин⁻¹ имеет КПД близкий к максимальному для выбранной скорости воздушного полета V_a =18 м/с , η_p = 0.78, η_m =0.84

На рисунке 3в представлены кривые тяги винта в зависимости от частоты вращения для двух разных скоростей воздушного потока. При выбранной скорости 18 м/с винт создает достаточную тягу T=3 Н для поддержания установившегося горизонтального полета.

Согласно выражению (34) и рисунку 8а можем оценить мощность, потребляемую СУ, с учетом эффективности регулятора оборотов η_(ESC) ≈0.85 :

P_(СУ) =(((Q_m)/(K_V +i_0)))/(η_(ESC))V_(in) ≈110 ВТ | (35)

# 4 Бортовое оборудование

# Состав бортового оборудования

Используемое бортовое оборудование и номинальные мощности представлены в таблице 4

ПК H743-WING V3 | Mateksys ELRS | GPS M10Q-5883 | ПВД ASPD-4525 | Ebyte E32-433T30D | FPV камера с передатчиком | Сервопривод PDI-HV2006MG
0.8 Вт | 0.375 Вт | 0.065 Вт | 0.025 Вт | 3 Вт | 0.2 Вт | 10 Вт

Таблица 4 – Список бортового оборудования

Структурная схема БО представлена рисунке 9

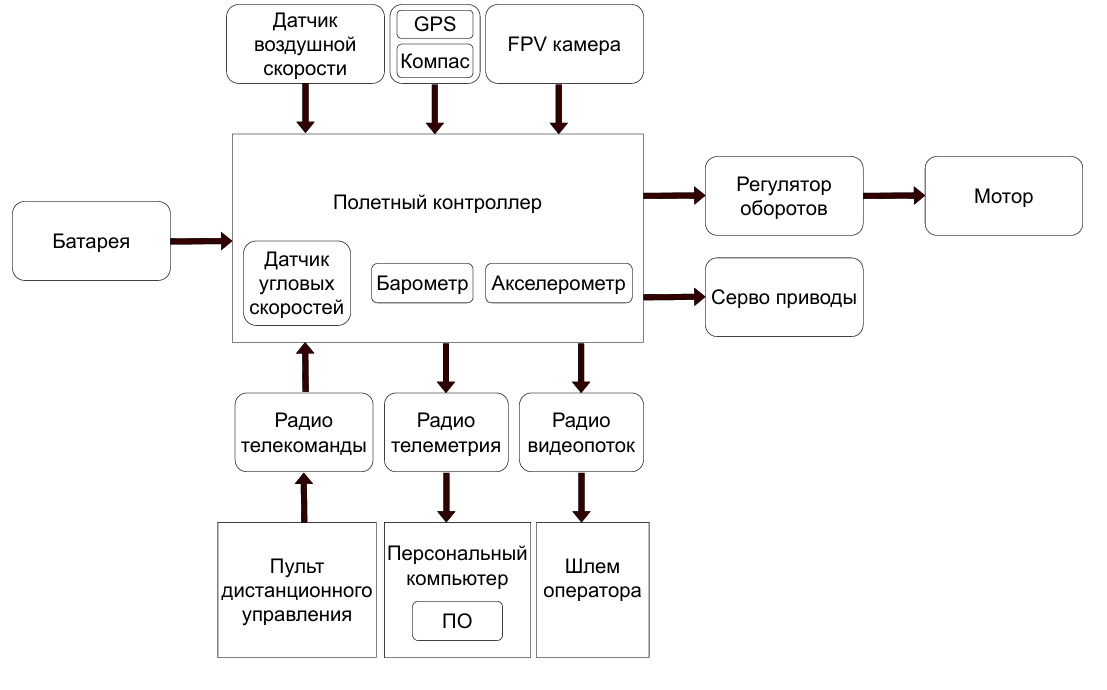
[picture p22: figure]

Рисунок 8 – Структурная схема бортового оборудования

# Система питания

Согласно расчетам СУ и таблице 4 суммарная потребляемая мощность ЛА в горизонтальном полете составила P_(∑) = P_(СУ) +P_(БО) ≈ 130 Вт . Для того чтобы находиться воздухе в течение t=0.5 ч , необходима энергия с запасом в 10% равная:

| E=1.1P_(∑) t≈ 72 Вт⋅ч | (36)

Таким образом, сборка 4S2P из Li-ion батарей Molicel типоразмера 18650 c характеристиками, представленными в таблице 5, являются подходящими для системы питания ЛА.

Емкость ячейки, А⋅ч | Номинальное напряжение, В | Масса ячейки, г | Удельная энергия сборки, Вт⋅ч/кг
2.8 | 3.7 | 50 | 185

Таблица 5 – Характеристики системы питания ЛА

Тогда расчетное время полета равно

| t_(полета) = (Удельная энергия×масса батарей)/(P_(∑))= (185⋅0.4)/130⋅60= 34 мин. | (37)

# Разрабатываемые аппаратная и программная части

Полетный контроллер решает задачи сбора телеметрии с внутренних датчиков и внешних модулей, обработки данных и выдачи управляющих воздействий на двигатель и рули управления. Полетный контроллер состоит из двух плат, плата коммутации питания и плата БВМ. Плата коммутации питания преобразует напряжение с батареи 12-24В в 5В и 3.3В, необходимых для работы периферийных устройств внутренних датчиков и основного вычислителя. Платы соединены друг с другом по принципу стека (рисунок 10), что позволило уменьшить размеры полетного контроллера. К внутренним датчикам, расположенным на плате БВМ относятся датчик абсолютного давления (BMP280), акселерометр и гироскоп (MPU9250). Также к БВМ подключаются внешние датчики, такие как ГНСС, ПВД. Для сохранения телеметрии на борту используется внешнее запоминающее устройство. БРК реализован в виде отдельного модуля. Высокопроизводительный контроллер STM32F405RGT6 с внешним кварцевым резонатором частотой 100 МГц позволяет реализовывать своевременную обработку данных со всех датчиков и вести расчёт управляющих воздействий, частота выдачи значений от датчиков зависит от установленной внутренней синхронизации, максимальная частота которой составляет 400 Гц . Четыре канала таймеров используются в режиме ШИМ модуляции для управления положением управляющих рулей, ещё два для работы с основным двигателем и активации системы спасения.

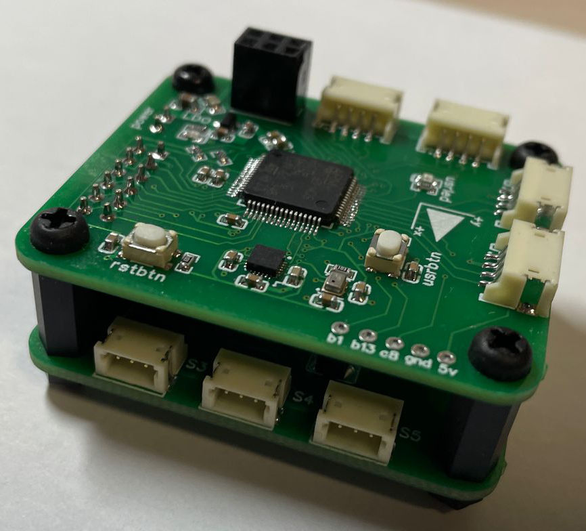
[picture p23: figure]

Рисунок 9 – Прототип полетного контроллера

# 5 Эксплуатационные ограничения

# Центровка

В качестве критерия примем условие устойчивости в продольном канале C_M =0 в режиме посадки (5°≥α≥3°) на скорости сваливания V_s =√((2W)/(ρSC_(Lmax))) . Задавая массу ЛА и положение центра масс, построим серию графиков балансировочных кривых (рисунок 11)

Рассмотрим один такой график. Начиная с некоторого значения положение центра масс, выбранному диапазону углов атаки не будет соответствовать пересечение нулевого уровня ни с одной из балансировочных кривых. Выбранное значение примем в качестве предельно передней центровки для массы, соответствующей графику. Проделывая аналогичные действия для масс ЛА в пределах 2.8 - 3.5 кг (задаваемых максимальной взлётной массой

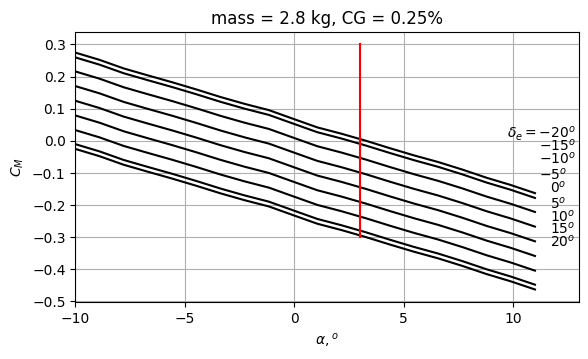
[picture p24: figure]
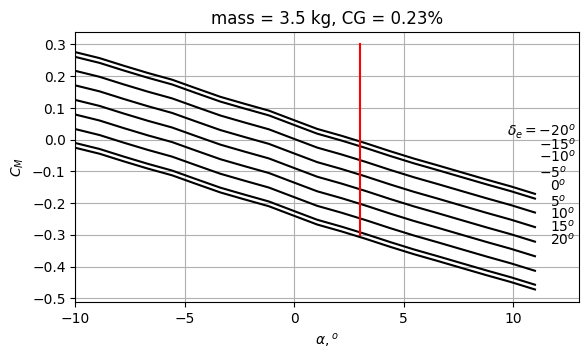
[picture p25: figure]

а) | б)

Рисунок 10 – балансировочные кривые для а) m=2.8 кг x_(цм) =0.25 б) m=3.5 кг x_(цм) =0.23

3.5 кг, наличием/отсутствием сбрасываемого груза 0.5 кг и неопределённостью в массе судейского трекера 0.15 - 0.2 кг) получим серию точек, проведем через них кривую на центровочной ведомости. В нашем случае центр масс смещается всего на 2% САХ, поэтому проведём прямую по двум точкам (для предельных масс). Полученная прямая является оценкой предельно передней центровки.

Оценку предельно задней центровки примем как положение центра давления (при α=3^o ) x_(цд) =0.53 . Таким образом, ограничивая положение центра масс на расстоянии не ближе 5% САХ от центра давления, мы получаем следующий вид центровочной кривой (рисунок 12)


Рисунок 11 – Центровочная кривая ЛА

# V-n диаграмма

Согласно [7] максимальные положительная и отрицательная перегрузки равны n_(+) =3.8, n_(-) = -1 . Согласно требованиям, указанным в [7] была построена V-n диаграмма на рисунке 12, где отображены V_s , V_A , V_C , V_D , скорость сваливания, маневренная скорость, скорость горизонтального полета ЛА и скорость пикирования соответственно. Также выделен участок диаграммы, характеризующий перегрузки при совместном отклонении элеронов при запуске с рук.

# 6 Цифровая модель динамики ЛА

Во время проектирования ЛА команда параллельно занималась разработкой численной динамической модели ЛА в среде MATLAB Simulink. Создание динамической модели было признано необходимым для экономии материальных и временных ресурсов команды, так как она позволяет проводить испытания ЛА в компьютерной среде при различных условиях и режимах полета, в том числе представляющих опасность для сохранности ЛА и его компонентов. Кроме того, компьютерное моделирование предоставляет возможность ещё на стадии разработки получить представление о поведении ЛА, что дает возможность внести необходимые изменения без необходимости изготовления летного образца. Так же создание численной динамической модели является одним из шагов на пути к созданию собственного автопилота.

За основу была взята нелинейная модель динамики ЛА с 6 степенями свободы, приведенная в [5]. Вектор состояния ЛА содержит 12 фазовых переменных — по три для каждого из векторов: координат в инерциальной системе координат (ИСК), скоростей в связанной системе координат (ССК), углов ориентации (углов Крылова) и угловых скоростей в ССК (38).

| x=(p_n p_e p_d u v w ϕ θ ψ p q r)^T | (19)

Были реализованы: модель постоянного ветра, кинематика и динамика поступательного и вращательного движения ЛА, модель электродвигателя с пропеллером согласно [5] и (30-34). В дальнейшем планируется добавить модель порывистого ветра и начать работу над созданием собственного автопилота.

Во время разработки ЛА проводились численные моделирования для верификации в компьютерной среде принятых аэродинамических решений. В частности, было проведено моделирование взлета ЛА при различных начальных условиях. В ходе моделирования начальная высота ЛА H0 принималась равной 2 м, начальная скорость ЛА V0 перебиралась в диапазоне 5–8 м/с. Так как на данном этапе разработки модели алгоритм управления ЛА отсутствует, динамика вращательного движения в данном моделировании не рассчитывалась, и угол тангажа принимался фиксированным на протяжении всего полета, перебираясь среди значений 0°, +5°, +10°, +15°. Скважность широтно-импульсно модулируемого (ШИМ) сигнала δ_t , отвечающего за величину подаваемого на электродвигатель напряжения V_(in) , принимала значения от 0.6 до 1.0. В процессе моделирования измерялась минимальная достигнутая ЛА высота. Полученные данные представлены в виде графиков на рисунке 13. Сплошным линиям соответствуют моделирования, где угол атаки ЛА не превышал 15°, что соответствует относительно линейному участку C_L (α) , пунктирным — где угол атаки не превышал 20°, т.е. где C_L (α) может вести себя нелинейным образом. Из результатов моделирования следует, что ЛА может взлетать как и с несколько меньшей скоростью метания, чем была определена в ходе эксперимента (2), так и с меньшей тягой. Так же стоит отметить, что при запуске ЛА с рук следует стараться создать ему положительный угол тангажа для наиболее надежного взлета, однако при моделировании была обнаружена закономерность: чем больший фиксированный угол тангажа имеет ЛА, тем большего угла атаки он достигает в ходе полета. В реальных условиях это приводит к необходимости использования такой системы управления, которая была бы способна удерживать угол атаки в оптимальном для ЛА диапазоне, независимо от стартового тангажа. В условиях текущего моделирования это влияет на соответствие полученных результатов реальному поведению ЛА — при больших углах атаки C_L (α) перестает вести себя линейным образом.


Рисунок 12 V-n диаграмма


Рисунок 13 - Графики минимальных достигнутых высот полета ЛА в зависимости от начальной скорости, скважности ШИМ и угла тангажа


Рисунок 14 - Моделирование при условиях: H0 = 2 м, V0 = 6 м/с, угол тангажа +5°, скважность ШИМ равна 1. Показаны графики координат и проекций скорости в ИСК по осям N, D («север», «вниз») от времени

# 7 Технология производства

# Материалы конструкции

В качестве основных материалов конструкции будут использоваться композитонаполненные пластики для 3Д печати (PETG), из которых планируется изготовить силовой набор шпангоутов. Пултрузионные угольные трубки для изготовления хвостовой балки и лонжеронов крыла. XPS пенопласт, покрытый стекловолокном для крыла. Фюзеляж для прототипа предполагается изготавливать методом 3Д печати, для конкурсного образца – из стеклопластика.

# Технология производства элементов конструкции

Как было упомянуто выше, в ходе производства ЛА предполагается использовать технологию 3Д печати, а также ЧПУ резчик по пенопласту для изготовления крыла, формование матриц для изготовления несущей обшивки крыла и элементов фюзеляжа для конкурсного образца.

# 8 График работ

График работ прилагается по ссылке (https://disk.yandex.ru/d/HnMQzW_9t9-L6A)

# 9 Список источников

[1] DATCOM

[2] General Aviation Design procedure

[3] Aircraft design conceptual approach

[4] Low Speed airfoil data V1

[5] Small UAV

[6] UIUC

[7] АП25

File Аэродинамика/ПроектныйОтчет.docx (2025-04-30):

## Проектный отчет команды «КБ-102»

# 1 Список сокращений и обозначений

α-угол атаки ЛА | V_a -скорость ЛА относительно воздушного потока | δ_e -угол отклонения управляющих поверхностей
C_l -коэффициент подъемной силы профиля | S_(w,t) -площадь крыла, хвостового оперения | C_(L_i ,D_i ,M_i) -производная аэродинамического коэффциента по параметру i
C_L -коэффициент подъемной силы ЛА | b-размах | λ-сужение
C_D -коэффициент силы лобового сопротивления ЛА | с-средняя аэродинамическая хорда | с_r -корневая хорда крыла
W-вес ЛА | i_w -угол установки крыла | A-удлинение
Λ_(с/2,c/4) - угол стреловидности линии половины и четверти крыла | k= (C_l)/(2π) | β^2 = 1-M^2 , M-число Маха
ПВД – приемник воздушного давления | ВПО – встроенное программное обеспечение | БВМ – бортовой вычислительный модуль

Команда использует обозначения согласно ISO 1151, чтобы иметь соответствие с обозначениями принятыми в модели динамики ЛА, разрабатываемой командой.

# 2 Аэродинамический облик

В ходе проектирования аэродинамического облика ЛА команда использовала инженерные методы оценки на основе экспериментальных данных, приведенных в [1, 2, 3]. Не смотря на то, что в источнике [1] числа Рейнольдса, при которых проводились эксперимент, выше, чем те, при которых будет эксплуатироваться разрабатываемый ЛА; приводимые оценки отражают динамику изменения аэродинамических характеристик ЛА. Был написан Python код, включающий в себя все выражения и взаимосвязи, описанные в данном разделе. Это позволило быстро оценивать аэродинамические характеристики ЛА по изменению входных данных: геометрия ЛА, масса, типы аэродинамических профилей и т.д.

После того, как аэродинамический облик был сформирован, были использованы методы численного моделирования для уточнения параметров и приведения их в соответствие с требуемыми значениями для выполнения ТЗ.

# Фюзеляж

Выбор формы фюзеляжа и его геометрических размеров (рисунок 1) основан на оценке места, занимаемого БО и грузом; а также на простоте в построении геометрии и в дальнейшем изготовлении. Для размещения необходимых элементов был выбран круговой профиль в поперечном сечении фюзеляжа, что также обеспечивает лучшие аэродинамические характеристики по сравнению с прямоугольным при таком же миделевом сечении. Длина фюзеляжа составила 1300 мм


Рисунок 1 – Общий вид ЛА

# Аэродинамические профили

На основе оценок атласа низкоскоростных профилей [4] был выбран SD7032 для крыла, обладающий приемлемыми характеристиками: спроектирован для эксплуатации на низких числах Рейнольдса (300 000), имеет плавную зависимость C_l (α) на закритическом режиме, высокое аэродинамическое качество.

Особенностью симметричных профилей на низких скоростях является нелинейный характер зависимости коэффициента подъемной силы от угла атаки вблизи α=0° [4, стр. 40]. Однако анализ ряда профилей показал в ходе исследования статической устойчивости, что нелинейности не оказывают существенного влияния на способность ЛА удерживать заданный угол атаки в широком диапазоне. Для хвостового оперения был выбран симметричный NACA0008.

# Геометрические характеристики крыла

Начальная оценка потребной площади крыла и его геометрических характеристик основывалась на предположении, что крыло должно создавать необходимую подъемную силу для компенсирования веса ЛА при заданной скорости горизонтального полета V_a =18 м/с , так как геометрические характеристики хвостового оперения и фюзеляжа и их вклад в C_L и C_D еще не определен. Тогда оценка для площади крыла имеет вид:

| S= (2W)/(ρV_a^2 C_L)= (2⋅35)/(1.225⋅18^2 ⋅0.5)=0.352 м^2 | (1)

Где C_L был выбран равным 0.5, как целевой коэффициент подъемной силы в горизонтальном полете, который будет в дальнейшем уточнен и оценен из характеристик построенной геометрии ЛА.

Скорость сваливания является важным показателем для оценки потребной площади крыла, его геометрических характеристик и размеров управляющих поверхностей, так как они влияют на достижимый максимальный коэффициент подъемной силы всего ЛА C_(L_(max)) , определяющий значение скорости сваливания. Для оценки скорости, сообщаемой человеком при запуске с рук V_0 , был проведен эксперимент, в ходе которого на скоростную съемку был записан момент броска объекта массой 3.5 кг. Из анализа видеозаписи была вычислена V_0 :

| V_0 = 7-8 м/c | (2)

Геометрические характеристики крыла представлены в таблице 1:

A | λ, м | b, м | c, м | c_r , м | S, м^2 | i_w , °
8 | 0.750 | 1.678 | 0.210 | 0.236 | 0.352 | 1.8

Таблица 1 – Геометрические характеристики крыла

# Хвостовое оперение

Для оценки площади хвостового оперения (ХО) воспользуемся методом объёмных коэффициентов ([1] стр. 158-161). В нашем случае ХО имеет V-образный тип, поэтому под горизонтальным (HT) и вертикальным (VT) ХО будем понимать проекции ХО на горизонтальную и вертикальную плоскости соответственно.

Согласно ([1], стр. 160) примем объёмные коэффициенты вертикального и горизонтального оперений c_(HT) =0.6, c_(VT) =0.04 . Возьмём плечо момента рыскания, создаваемого вертикальным оперением L_(VT) равным плечу момента тангажа, создаваемого горизонтальным оперением L_(HT) и равным L≈0.8м . Тогда площади вертикального и горизонтального оперений равны

| S_(VT) =(c_(VT) bS)/(L_(VT))≈0.029м^2 , S_(HT) =(c_(HT) cS)/(L_(HT))≈0.055м^2 | (3)

Их сумма даёт полную площадь хвостового оперения S_T =S_(HT) +S_(VT) ≈0.085м^2 . Угол наклона одной лопатки относительно горизонтальной плоскости Γ=arctg((S_(VT))/(S_(HT)))≈28^o , тогда угол раствора лопаток. Геометрические характеристики ХО представлены в таблице 2

S_t , м^2 | λ_t | A_t | b_t , м | c, м | c_r^t , м | Γ, °
0.085 | 0.6 | 2 | 0.291 | 0.146 | 0.182 | 28

Таблица 2 – Геометрические характеристики хвостового оперения

# Управляющие поверхности

Размер управляющих поверхностей и доля размаха хвостового оперения и крыла, занимаемого ими, указаны в таблице 3.

| Элероны | Руль высоты
Доля хорды ( c_f /c ) | 0.3 | 0.3
Доля размаха ( b_f /b ) | 0.5 | 0.8

Таблица 3 – Характеристики управляющих поверхностей

Выбор такой геометрии обусловлен тем, что предельная эффективность управляющих поверхностей (максимальный прирост ΔC_L за счет отклонения рулей) (рисунок 2) достигается при небольших углах отклонения рулей до 20°÷25° . Более того, как будет показано далее, такая конфигурация обеспечивает статическую устойчивость в продольном канале ЛА.

# Модель коэффициента подъемной силы

Для оценки C_L всего ЛА была рассмотрена модель коэффициента подъемной силы согласно источнику [5]:

| C_L (α, δ_e , q)=C_(L_0) +C_(L_α) α+C_(L_(δ_e)) δ_e +C_(L_q) c/(2V_a)q | (4)

Последовательно оценим вклад крыла и хвостового оперения в каждое слагаемое в (4), кроме последнего, так как в данном отчете рассматривается лишь стационарный полет ЛА, подразумевающий p=q=r=0 .

Второе слагаемое состоит из вклада хвостового оперения и крыла при δ_e =0 . Согласно [1] C_(L_α) можно оценить следующим образом, учитывая геометрию крыла:

| C_(L_α) = (2πA)/(2+ √((A^2 β^2)/(k^2 (α))(1+ (tg^2 (Λ_(c/2) ))/(β^2))+4)) | (5)

Таким образом, второе слагаемое в (4) имеет вид:

| C_(L_α) (α)α≈C_(L_α) α=(C_(L_α)^w +(S_(ht))/SC_(L_α)^t )α=(4.71+ 0.053/0.3522.87)α= 5.14α | (6)

Первое слагаемое в (4) вновь включает вклад крыла и хвостового оперения. Для оценки значения C_(L_0) воспользуемся методом, описанным в [2], предполагающий отсутствие изменения в угле атаки α_0 , при котором C_l (α_0 )=C_L _0 (α_0 )=0 .

| C_(l_0) =-α_0 C_(l_α) , α_0 = -(C_(l_0))/(C_(l_α)) | (7)

| C_(L_0) =|α_0 |C_(L_a) = |(C_(l_0))/(C_(l_α))|C_(L_a) | (8)

С учетом полученного выражения (8) получим первое слагаемое из (4), которое имеет вид:

| C_(L_0) =С_(L_0)^w + (S_(ht))/SC_(L_0)^t =0.498+ 0.053/0.3520.0=0.498 | (9)

Наконец оценим вклад третьего слагаемого в (4). Для его определения был использован метод, представленный в [1], предполагающий оценку влияния отклонения управляющих поверхностей на C_l для крыла бесконечного размаха фиксированного профиля (10), а затем учет геометрических характеристик крыла для вычисления приращения коэффициента подъемной силы ΔC_L за счет отклонения рулевых поверхностей (11).

| ΔC_l =δ((C_(l_δ))/((C_(l_δ) )_(теор)))(C_(l_δ) )_(теор) K^(') | (10)

| ΔC_L =ΔC_l ((C_(L_α))/(C_(l_α)))mK_b = δ((C_(l_δ))/((C_(l_δ) )_(теор)))(C_(l_δ) )_(теор) K^(') ((C_(L_α))/(C_(l_α)))mK_b | (11)

где K^(') и K_b – экспериментальные поправочные коэффициенты для эффективности подъемной силы за счет отклонения управляющих поверхностей и доли площади крыла, занимаемой управляющими поверхностями, соответственно. На рисунке 2 изображен вклад хвостового оперения и крыла в C_L при отклонении управляющих поверхностей согласно выражению (11). Приведем также численное значение третьего слагаемого в выражении (4) за счет отклонения управляющих поверхностей хвостового оперения в области углов отклонения δ_e = -15°÷15° , где зависимость линейна (рисунок 2)

| C_(L_(δ_e)) δ_e =0.08δ_e | (12)

Отметим, что на рисунке 3 кривая для крыла была построена в предположении совместного отклонения элеронов, например при старте с рук, когда есть возможность их совместного отклонения для увеличения подъемной силы крыла. В горизонтальном полете, когда функция элеронов – управлять креном, представленная зависимость не применима. Однако зависимость может быть обобщена для закрылков, если таковые появятся в конструкции в последующем.


Рисунок 2 – Приращение коэффициента подъемной силы ЛА за счет отклонения управляющих поверхностей крыла и хвостового оперения

Приведем окончательный вид зависимость коэффициента подъемной силы всего ЛА в случае стационарного полета:

| C_L (α, δ_e )=0.498+5.14α+0.08δ_e | (13)

# Модель коэффициента силы лобового сопротивления

Необходимость в оценке силы сопротивления, действующей на ЛА, обусловлена ее необходимостью для определения подходящей силовой установки и дальнейшего выбора системы питания и оценки продолжительности полета.

Согласно источнику [5] модель коэффициента лобового сопротивления ЛА имеет вид:

| C_D (α, δ_e , q)=C_(D_0) +C_(D_α) α+C_(D_(δ_e)) δ_e +C_(D_q) c/(2V_a)q | (14)

Коэффициент силы лобового сопротивления за счет сил трения C_(D_0) согласно [2] можно оценить, как сумму коэффициентов сил трения элементов конструкции ЛА.

| C_(D_0) =(C_(D_(add)) + 1/S∑_i C_(f_i) ⋅FF_i ⋅S_(wet_i) ⋅IF_i )k_(кэнс) | (15)

где C_f – коэффициент сил трения, FF – множитель, учитывающий форму обтекаемого тела, IF – множитель, учитывающий взаимное расположение и влияние элементов конструкции друг на друга, S_(wet) – полная площадь поверхности элемента, подверженная обтеканию воздушным потоком, C_(D_(add)) - дополнительный коэффициент сопротивления за счет элементов конструкции, не являющихся крылом или фюзеляжем, например, подвесных конструкций на крыле, k_(кэнс) – множитель кумулятивного эффекта нежелательного сопротивления, учитывающий неидеальность конструкции и отличие расчетных форм от действительных

Согласно выражению (15) был проведен подсчет вклада фюзеляжа, крыла и хвостового оперения в C_(D_0) . Для оценки C_f каждого компонента была использована модель турбулентно-ламинарного обтекания тела [2], имеющая следующий вид:

| (x_0)/l=36.9((x_(tr))/l)^0.625 (1/(Re))^0.375 | (16)

| C_f = 0.074/(Re^0.2)(1-((x_(tr) -x_0)/l))^0.8 | (17)

где x_0 – приведенная точка перехода от ламинарного к турбулентному обтеканию тела, x_(tr) – точка перехода от ламинарного к турбулентному режиму обтеканию тела. И x_0 и x_(tr) отсчитываются от передних кромок обтекаемых потоком тел. l – характерная длина обтекаемого тела (хорда крыла, длина фюзеляжа)

Для профиля крыла и хвостового оперения значения x_(tr) были взяты из результатов их анализа в программе XFOIL при Re=300 000 . Для фюзеляжа было принято для всех углов атаки (x_(tr))/l=0.05

| C_(D_0) (Re=300 000)= 0.024 | (18)

Параметр k_(кэнс) согласно [2] имеет значение 1.25 . Результат подсчета вклада первых двух слагаемых в (14) представлен в виде столбчатой диаграммы на рисунке 3.

Для более точной оценки лобового сопротивления в зависимости от угла атаки и геометрических характеристик ЛА используем дополненную квадратичную модель коэффициента лобового сопротивления. Второе слагаемое в (14) заменим следующим образом:


Рисунок 3 – Покомпонентный вклад в коэффициент лобового сопротивления элементов конструкции и индуцированное сопротивление в горизонтальном полете и при взлете

| C_(D_α) α=C_(D_i) (α)= ((C_L (α)-C_(LminD) )^2)/(πeA) | (19)

Коэффициент эффективности Освальда был оценен согласно выражению из [2]:

| e= 1/(π⋅A⋅r⋅C_(D_0) +1/(((1+0.03t-2t^2 )u)))=0.78 | (20)

где u=0.98 , r=0.38- (Λ_0)/3000+ (Λ_0^2)/15000

| C_(D_α) =(∂C_(D_i))/(∂α)=2/(πeA)(C_(L_0) +C_(L_α) α-C_(LminD) )C_(L_α) =10.28/19.6(0.5+5.14α-0.5)=2.7α | (21)

Так же приведем зависимость индуцированного и сопротивления трения от воздушной скорости (рисунок 4). По нему определим оптимальную скорость горизонтального полета с наименьшей силой лобового сопротивления.


Рисунок 4 – Зависимость сопротивления трения и индуцированного от воздушной скорости в горизонтальном полете

Видим, что оптимальная скорость полета, обеспечивающая наибольшее время полета равна 16 м/с . Однако для преодоления маршрута длиной 20 км за оценочное время 20 минут была выбрана скорость горизонтального полета 18 м/c

В качестве оценки третьего слагаемого в (14) примем оценку C_(D_(δ_e)) =0.006 согласно [2]. Тогда окончательное выражение для коэффициента лобового сопротивления имеет вид

| C_D (α, δ_e )=0.024+2.7α^2 +0.006δ_e | (22)

# Модель коэффициента момента тангажа

Рассмотрим модель момента тангажа следующего вида:

| C_M =C_(M_0) +C_(M_α) α+C_(M_(δ_e)) δ_e | (23)

Вновь последовательно оценим вклад СУ, крыла и хвостового оперения в три слагаемых выше. Первое слагаемое есть сумма вида: C_(M_0) =C_(M_0)^w +C_(M_0)^t +C_(M_0)^(prop) . Согласно [3] имеем:

| C_(M_0)^w = C_(m_0)^w ((Acos^2 Λ_(c/4))/(A+2cosΛ_(c/4))) + C_(L_0)^w ((l_(cg)^w)/c)= 0.002 | (24)
| C_(M_0)^t =(C_(m_0)^t ((Acos^2 Λ_(c/4))/(A+2cosΛ_(c/4)))((c_(tail))/c)+C_(L_0)^t ((l_(cg)^t)/c))((S_(ht))/S)= 0 | (25)

C_(M_0)^t =0 , так как профиль симметричный и угол установки хвостового оперения равен 0. Вклад СУ с учетом расположения линии тяги выше центра масс имеет вид

| C_(M_0)^(prop) = (2r_m ×T)/(ρV_a^2 Sc)= -(2z_m T)/(ρV_a^2 Sc)= -(2⋅0.03⋅2.6)/(1.225⋅18^2 ⋅0.352⋅0.21)= -0.005 | (26)

Для второго слагаемого в (23) c учетом отклонения крылом набегающего потока и ослаблением его (∂ϵ)/(∂α)=0.1, η=0.9 запишем:

| C_(M_α) = C_(M_α)^w +C_(M_α)^t =C_(L_α)^w ((l_(cg)^w)/c)-η ((S_(ht))/S)C_(L_0)^t ((l_(cg)^t)/c)(1- (∂ϵ)/(∂α))=-0.561 | (27)

Наконец оценим третье слагаемое в (23):

| C_(M_(δ_e)) = -ηC_(L_(δ_e)) ((S_(ht))/S)((l_(cg)^t)/c)= -0.456 | (28)

Приведем окончательный вид зависимости модели коэффициента момента тангажа:

| C_(M_(δ_e)) = -0.003-0.561α-0.456δ_e | (29)

# Статическая устойчивость ЛА в продольном канале

Для анализа ЛА на статическую устойчивость в продольном канале в зависимости от центровки и геометрических характеристик было вычислено положение центра давления и схематически нанесено на рисунке 5. Было найдено оптимальное положение центра масс ЛА, при котором возможен установившийся горизонтальный полет без отклоненных рулей хвостового оперения при массе ЛА 3.5 кг. На основе модели коэффициента момента тангажа (29), которая была получена для оптимального положения центра масс на расстоянии от передней кромки крыла x_(cg) =0.4c , были построены балансировочные кривые (рисунок 6). Балансировочные кривые имеют отрицательный наклон, что говорит о статической устойчивости ЛА в продольном канале

Рисунок 5 – Схематичное положение ЦМ – центра масс, ЦД – центра давления и АЦ – аэродинамического центра крыла

Однако из-за нелинейности прироста как коэффициента подъемной силы, так и момента тангажа за счет отклонения управляющих поверхностей стоит увеличить |C_(M_α) | для большей статической устойчивости согласно (27) путем увеличения размеров хвостового оперения, длины плеча хвостового оперения или же передней центровкой ЛА.


Рисунок 6 – Балансировочные кривые для координаты центра масс x_(cg) =0.4c

# 3 Силовая установка

# Выбор воздушного винта

Подход к выбору формы и размера пропеллера основан на экспериментальных данных, полученных при испытании воздушных винтов в аэродинамической трубе [6]. Команда выбирала пропеллеры, которые бы давали необходимую тягу для выбранной скорости горизонтального полета с диапазоном частот вращения, который включен в набор угловых скоростей вращения в экспериментальных данных ( 3000÷6000 мин^(-1) ) [6], чтобы быть уверенными в полученных командой оценках. Согласно теории [5 стр. 52], разработанной для оценки тяги и механического момента винта, их выражения имеют следующий вид:

| T= (ρD^4)/(4π^2)Ω^2 C_T | (30)
| Q_p = (ρD^5)/(4π^2)Ω^2 C_Q | (31)

Безразмерные коэффициенты тяги и момента винта могут быть разложены в ряд по степеням поступи винта J= (2πV_a)/(ΩD) (32-33). Согласно рисунку 4 требуемая тяга для поддержания горизонтального полета T=2.5÷3 Н . В ходе анализа различных воздушных винтов, удовлетворяющих требованиям потребной тяги, был выбран винт AeroNaut 11x8.

| C_T =C_(T_0) +C_(T_1) J+C_(T_2) J^2 | (32)
| C_Q =C_(Q_0) +C_(Q_1) J+C_(Q_2) J^2 | (33)


Рисунок 7 - Выбор оптимальных параметров мотора X2814 и винта AeroNaut 11x8 при горизонтальном полете V_a =18 м/с . а) – пересечение кривых моментов винта и мотора. б) – кривые эффективности мотора и винта. в) – кривые тяги винта. Вертикальная пунктирная линия указывает рабочую частоту вращения

# 3.1 Выбор мотора

В ходе анализа ряда моторов был выбран Sunnysky X2814 900 kv, так как он оптимален по потребляемой мощности для всех рассматриваемых воздушных винтов. Согласно [5 стр. 53] из равенства механических моментов винта и мотора была найдена точка пересечения кривых моментов винта и мотора (рисунок 8а), соответствующая угловой скорости вращения 5800 мин⁻¹.

Q_m =K_Q (((V_(in) -K_V Ω))/(R-i_0)) | (34)

Также были построены кривые КПД мотора и винта на рисунке 8б, чтобы убедиться в оптимальном режиме работы ВМГ в выбранном диапазоне угловых частот вращения. Как видно на рисунке 8б, и мотор, и винт на частоте 5800 мин⁻¹ имеет КПД близкий к максимальному для выбранной скорости воздушного полета V_a =18 м/с , η_p = 0.78, η_m =0.84

На рисунке 3в представлены кривые тяги винта в зависимости от частоты вращения для двух разных скоростей воздушного потока. При выбранной скорости 18 м/с винт создает достаточную тягу T=3 Н для поддержания установившегося горизонтального полета.

Согласно выражению (34) и рисунку 8а можем оценить мощность, потребляемую СУ, с учетом эффективности регулятора оборотов η_(ESC) ≈0.85 :

P_(СУ) =(((Q_m)/(K_V +i_0)))/(η_(ESC))V_(in) ≈110 ВТ | (35)

# 4 Бортовое оборудование

# Состав бортового оборудования

Используемое бортовое оборудование и номинальные мощности представлены в таблице 4

ПК H743-WING V3 | Mateksys ELRS | GPS M10Q-5883 | ПВД ASPD-4525 | Ebyte E32-433T30D | FPV камера с передатчиком | Сервопривод PDI-HV2006MG
0.8 Вт | 0.375 Вт | 0.065 Вт | 0.025 Вт | 3 Вт | 0.2 Вт | 10 Вт

Таблица 4 – Список бортового оборудования

Структурная схема БО представлена рисунке 9


Рисунок 8 – Структурная схема бортового оборудования

# Система питания

Согласно расчетам СУ и таблице 4 суммарная потребляемая мощность ЛА в горизонтальном полете составила P_(∑) = P_(СУ) +P_(БО) ≈ 130 Вт . Для того чтобы находиться воздухе в течение t=0.5 ч , необходима энергия с запасом в 10% равная:

| E=1.1P_(∑) t≈ 72 Вт⋅ч | (36)

Таким образом, сборка 4S2P из Li-ion батарей Molicel типоразмера 18650 c характеристиками, представленными в таблице 5, являются подходящими для системы питания ЛА.

Емкость ячейки, А⋅ч | Номинальное напряжение, В | Масса ячейки, г | Удельная энергия сборки, Вт⋅ч/кг
2.8 | 3.7 | 50 | 185

Таблица 5 – Характеристики системы питания ЛА

Тогда расчетное время полета равно

| t_(полета) = (Удельная энергия×масса батарей)/(P_(∑))= (185⋅0.4)/130⋅60= 34 мин. | (37)

# Разрабатываемые аппаратная и программная части

Полетный контроллер решает задачи сбора телеметрии с внутренних датчиков и внешних модулей, обработки данных и выдачи управляющих воздействий на двигатель и рули управления. Полетный контроллер состоит из двух плат, плата коммутации питания и плата БВМ. Плата коммутации питания преобразует напряжение с батареи 12-24В в 5В и 3.3В, необходимых для работы периферийных устройств внутренних датчиков и основного вычислителя. Платы соединены друг с другом по принципу стека (рисунок 10), что позволило уменьшить размеры полетного контроллера. К внутренним датчикам, расположенным на плате БВМ относятся датчик абсолютного давления (BMP280), акселерометр и гироскоп (MPU9250). Также к БВМ подключаются внешние датчики, такие как ГНСС, ПВД. Для сохранения телеметрии на борту используется внешнее запоминающее устройство. БРК реализован в виде отдельного модуля. Высокопроизводительный контроллер STM32F405RGT6 с внешним кварцевым резонатором частотой 100 МГц позволяет реализовывать своевременную обработку данных со всех датчиков и вести расчёт управляющих воздействий, частота выдачи значений от датчиков зависит от установленной внутренней синхронизации, максимальная частота которой составляет 400 Гц . Четыре канала таймеров используются в режиме ШИМ модуляции для управления положением управляющих рулей, ещё два для работы с основным двигателем и активации системы спасения.


Рисунок 9 – Прототип полетного контроллера

# 5 Эксплуатационные ограничения

# Центровка

В качестве критерия примем условие устойчивости в продольном канале C_M =0 в режиме посадки (5°≥α≥3°) на скорости сваливания V_s =√((2W)/(ρSC_(Lmax))) . Задавая массу ЛА и положение центра масс, построим серию графиков балансировочных кривых (рисунок 11)

Рассмотрим один такой график. Начиная с некоторого значения положение центра масс, выбранному диапазону углов атаки не будет соответствовать пересечение нулевого уровня ни с одной из балансировочных кривых. Выбранное значение примем в качестве предельно передней центровки для массы, соответствующей графику. Проделывая аналогичные действия для масс ЛА в пределах 2.8 - 3.5 кг (задаваемых максимальной взлётной массой


а) | б)

Рисунок 10 – балансировочные кривые для а) m=2.8 кг x_(цм) =0.25 б) m=3.5 кг x_(цм) =0.23

3.5 кг, наличием/отсутствием сбрасываемого груза 0.5 кг и неопределённостью в массе судейского трекера 0.15 - 0.2 кг) получим серию точек, проведем через них кривую на центровочной ведомости. В нашем случае центр масс смещается всего на 2% САХ, поэтому проведём прямую по двум точкам (для предельных масс). Полученная прямая является оценкой предельно передней центровки.

Оценку предельно задней центровки примем как положение центра давления (при α=3^o ) x_(цд) =0.53 . Таким образом, ограничивая положение центра масс на расстоянии не ближе 5% САХ от центра давления, мы получаем следующий вид центровочной кривой (рисунок 12)


Рисунок 11 – Центровочная кривая ЛА

# V-n диаграмма

Согласно [7] максимальные положительная и отрицательная перегрузки равны n_(+) =3.8, n_(-) = -1 . Согласно требованиям, указанным в [7] была построена V-n диаграмма на рисунке 12, где отображены V_s , V_A , V_C , V_D , скорость сваливания, маневренная скорость, скорость горизонтального полета ЛА и скорость пикирования соответственно. Также выделен участок диаграммы, характеризующий перегрузки при совместном отклонении элеронов при запуске с рук.

# 6 Цифровая модель динамики ЛА

Во время проектирования ЛА команда параллельно занималась разработкой численной динамической модели ЛА в среде MATLAB Simulink. Создание динамической модели было признано необходимым для экономии материальных и временных ресурсов команды, так как она позволяет проводить испытания ЛА в компьютерной среде при различных условиях и режимах полета, в том числе представляющих опасность для сохранности ЛА и его компонентов. Кроме того, компьютерное моделирование предоставляет возможность ещё на стадии разработки получить представление о поведении ЛА, что дает возможность внести необходимые изменения без необходимости изготовления летного образца. Так же создание численной динамической модели является одним из шагов на пути к созданию собственного автопилота.

За основу была взята нелинейная модель динамики ЛА с 6 степенями свободы, приведенная в [5]. Вектор состояния ЛА содержит 12 фазовых переменных — по три для каждого из векторов: координат в инерциальной системе координат (ИСК), скоростей в связанной системе координат (ССК), углов ориентации (углов Крылова) и угловых скоростей в ССК (38).

| x=(p_n p_e p_d u v w ϕ θ ψ p q r)^T | (19)

Были реализованы: модель постоянного ветра, кинематика и динамика поступательного и вращательного движения ЛА, модель электродвигателя с пропеллером согласно [5] и (30-34). В дальнейшем планируется добавить модель порывистого ветра и начать работу над созданием собственного автопилота.

Во время разработки ЛА проводились численные моделирования для верификации в компьютерной среде принятых аэродинамических решений. В частности, было проведено моделирование взлета ЛА при различных начальных условиях. В ходе моделирования начальная высота ЛА H0 принималась равной 2 м, начальная скорость ЛА V0 перебиралась в диапазоне 5–8 м/с. Так как на данном этапе разработки модели алгоритм управления ЛА отсутствует, динамика вращательного движения в данном моделировании не рассчитывалась, и угол тангажа принимался фиксированным на протяжении всего полета, перебираясь среди значений 0°, +5°, +10°, +15°. Скважность широтно-импульсно модулируемого (ШИМ) сигнала δ_t , отвечающего за величину подаваемого на электродвигатель напряжения V_(in) , принимала значения от 0.6 до 1.0. В процессе моделирования измерялась минимальная достигнутая ЛА высота. Полученные данные представлены в виде графиков на рисунке 13. Сплошным линиям соответствуют моделирования, где угол атаки ЛА не превышал 15°, что соответствует относительно линейному участку C_L (α) , пунктирным — где угол атаки не превышал 20°, т.е. где C_L (α) может вести себя нелинейным образом. Из результатов моделирования следует, что ЛА может взлетать как и с несколько меньшей скоростью метания, чем была определена в ходе эксперимента (2), так и с меньшей тягой. Так же стоит отметить, что при запуске ЛА с рук следует стараться создать ему положительный угол тангажа для наиболее надежного взлета, однако при моделировании была обнаружена закономерность: чем больший фиксированный угол тангажа имеет ЛА, тем большего угла атаки он достигает в ходе полета. В реальных условиях это приводит к необходимости использования такой системы управления, которая была бы способна удерживать угол атаки в оптимальном для ЛА диапазоне, независимо от стартового тангажа. В условиях текущего моделирования это влияет на соответствие полученных результатов реальному поведению ЛА — при больших углах атаки C_L (α) перестает вести себя линейным образом.


Рисунок 12 V-n диаграмма


Рисунок 13 - Графики минимальных достигнутых высот полета ЛА в зависимости от начальной скорости, скважности ШИМ и угла тангажа


Рисунок 14 - Моделирование при условиях: H0 = 2 м, V0 = 6 м/с, угол тангажа +5°, скважность ШИМ равна 1. Показаны графики координат и проекций скорости в ИСК по осям N, D («север», «вниз») от времени

# 7 Технология производства

# Материалы конструкции

В качестве основных материалов конструкции будут использоваться композитонаполненные пластики для 3Д печати (PETG), из которых планируется изготовить силовой набор шпангоутов. Пултрузионные угольные трубки для изготовления хвостовой балки и лонжеронов крыла. XPS пенопласт, покрытый стекловолокном для крыла. Фюзеляж для прототипа предполагается изготавливать методом 3Д печати, для конкурсного образца – из стеклопластика.

# Технология производства элементов конструкции

Как было упомянуто выше, в ходе производства ЛА предполагается использовать технологию 3Д печати, а также ЧПУ резчик по пенопласту для изготовления крыла, формование матриц для изготовления несущей обшивки крыла и элементов фюзеляжа для конкурсного образца.

# 8 График работ

График работ прилагается по ссылке (https://disk.yandex.ru/d/HnMQzW_9t9-L6A)

# 9 Список источников

[1] Hoak, D., and Ellison, D., et al., "USAF DATCOM"

[2] Snorri Gudmundsson, General Aviation Aircraft Design: Applied Methods and Procedures

[3] Daniel Raymer, Aircraft design a conceptual approach

[4] Low Speed airfoil data V1

[5] Randal W. Beard, Timothy W. McLain, Small Unmanned Aircraft: Theory and Practice

[6] UIUC Propeller Data Base

[7] АП25

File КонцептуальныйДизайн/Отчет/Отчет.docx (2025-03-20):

## Концептуальный отчет команды «КБ-102»

# 1 Команда


| Кулишов Александр – куратор Курирует процесс производства | | Бунаков Егор Разработка аппаратной и программной частей автопилота | | Сутурин Даниил – капитан Ведение документации


| Сериков Алексей Выбор и проектирование БО | | Огородников Егор Аэродинамические расчеты | | Максимов Руслан Разработка систем управления, навигации


| Волков Роман Разработка систем управления, навигации, компьютерного зрения | | Гончарова Диана Разработка систем управления, навигации | | Сериков Василий Интеграция БО и коммерческого полетного контроллера

# 2 Анализ технического задания и ограничений

# Выбор полетного задания

Командой было принято решение о выборе легкого маршрута длиной 20 км со сбросом груза. Так же будет вестись разработка системы компьютерного зрения. Приоритет в разработке отдан системе управления и грузоподъемности ЛА, поэтому акробатика не включена в полетное задание.

# Скорость горизонтального полета

Для прохождения маршрута длиной x = 20 км ([1] стр. 49) за t = 20 мин ([1] стр. 44) оценим среднюю скорость ЛА относительно земли υ_g =21м/с . Тогда в отсутствие ветра динамическое давление q=(ρυ_g^2)/2≈265(Па)/м

# 3 Предварительный облик летательного аппарата

# Аэродинамическая схема

Предполагается крепить крыло к верхней части фюзеляжа, т.к. это позволит уменьшить шанс повреждения крыла при крене в ходе посадки на днище. Прямоугольная форма крыла наиболее доступная в изготовлении. В качестве хвостового оперения рассматривается V-образная схема, так как проста в изготовлении и меньший риск при крене во время посадки зацепить поверхность. Команда пришла к решению о выборе одиночного тянущего винта в носовой части ЛА, что позволит безопасно запускать с рук ЛА и обеспечит обдув винтом крыла и охлаждение мотора набегающим воздухом.

# Оценка геометрических характеристик

Площадь крыла S=cb , где c – средняя аэродинамическая хорда, b – размах крыла. Возьмём удлинение крыла λ=(b^2)/S=b/c≈7 как наиболее распространённое значение для гражданских ЛА ([2] стр. 78). Также примем c≈20см , чтобы крыло помещалось в транспортировочную коробку 150см×35см×35см ([1] стр. 26). Таким образом, S=cb=7c^2 ≈0.28м^2 , b=1.4 м

Для возможности транспортировки груза внутри объема фюзеляжа, минимальные характерные размеры в сечении должны быть порядка 80×80 мм .

# Силовая установка и элементы питания

Потребная тяга горизонтального полёта T_(гп) =G/(K_(ЛА))≈0.35кгс , где K_(ЛА) ≈10 -аэродинамическое качество ЛА ([2] стр. 39 рис. 3.5)

Необходимую тягу в режиме набора высоты оценим следующим образом T_(под) =D+Gsin(γ)= T_(гп) + Gsin(γ)=1.26 кгс

На основе анализа выше был выбран мотор с характеристиками, приведенными в таблице

Модель | Максимальная мощность | Kv | Размер винта (дюймы)
AT2814 | 650 Ватт | 900 | 11х5.5

Таблица 1 – Характеристики мотора

Для обеспечения СУ и бортового оборудования необходимой мощностью в течении 20 минут полета предварительно был выбран литий полимерный аккумулятор типа 4S емкостью 6 А∙ч

# 4 Бортовое оборудование и программное обеспечение

# Аппаратная часть

На борту ЛА планируется расположить два полетных контроллера, один из которых коммерческий (Matek H743 Wing) будет создавать управляющие воздействия на рули управления и определять обороты двигателя, второй полетный контроллер – «пассажир» собственной разработки планируется использовать для сбора данных телеметрии и анализа выдающих им управляющих воздействий. В состав разрабатываемого аппаратного решения входят: блок инерциальной навигации, блок измерения магнитного поля, блок спутниковой навигации.

Контроллер полета будет взаимодействовать с такими внешними модулями как: коммерческий блок командно-телеметрической радио линии, использующий технологию модуляции LoRa, позволит передавать командно-телеметрическую информацию на расстоянии до 10 км; постоянно запоминающее устройство, а именно FLASH память для сохранения всей телеметрии полета.

# Программная часть

В качестве основного программного обеспечения для управления и автономной навигации будет выступать ArduPilot. Однако команда приняла решение о параллельной разработке своего полетного контроллера и автопилота. Предполагается, что на дальнейших стадиях разработки, в ходе которых будут определены аэродинамический облик и характеристики ЛА, динамическая модель ЛА будет взята за основу для синтеза и моделирования управления в среде динамического моделирования Matlab Simulink и дальнейшего переноса программы на язык C для реализации алгоритмов автопилота на базе разрабатываемой аппаратной части. В случае положительного результата макетирования разрабатываемого решения будет произведен сбор телеметрии с контроллера в режиме «пассажир» на борту ЛА. Если полет будет признан успешным (автопилот правильно сообщает управляющее воздействие), то дальнейший шаг – разрабатываемый контроллер и алгоритм становятся основной аппаратной и программной частью системы управления ЛА.

# Система компьютерного зрения

Так как ни один член команды не обладает достаточным опытом работы с системами компьютерного зрения, оценка трудоемкости затруднительна. По этой же причине в ходе коллективного обсуждения задача была признана неприоритетной, с допущением возможности её реализации при наличии свободных трудовых ресурсов. Система компьютерного зрения включает в себя видеокамеру для получения изображения, вычислитель для его обработки и распознавания на нём символов, а также кардридер с поддержкой MicroSD карт для сохранения данных. Необходимо будет разработать ПО для распознавания букв армянского алфавита: данную задачу предлагается решить с помощью свёрточной нейронной сети, на вход которой будет подаваться предобработанное изображение, содержащее лишь саму букву. Данный подход призван упростить процесс обучения нейронной сети. Географические координаты символа будут определяться с помощью его угловых координат, измеряемых камерой относительно ЛА, и местоположения самого ЛА, определяемого его навигационной системой.

# 5 Процесс разработки

Подход к проектированию ЛА представлен на рисунке 1.


Рисунок 1 – блок-схема процесса разработки ЛА


Рисунок 2 – Чертежный вид ЛА

# 6 График работ

Детализированный график работ с описанием задач и ответственных прилагается по ссылке (https://disk.yandex.ru/i/gJ8DDl-IPzN4OA).

# 7 Список источников

1. Положение о Студенческом конкурсе авиационного творчества (СКАТ) Основной трек
2. D.P. Raymer, Aircraft Design: A Conceptual Approach. AIAA, 2018. — 1062 c.

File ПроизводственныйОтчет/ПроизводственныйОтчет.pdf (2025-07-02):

Производственный отчет команды «КБ-102»

### Оглавление

Список сокращений и обозначений

ПВД – приемник воздушного

давления

ВПО – встроенное

программное обеспечение

БВМ – бортовой

вычислительный модуль

БИНС | – | бес

платформенная инерциальная

навигационная система

ЦУП | – | центр

управления полетом

ПИД | –

пропорционально

интегрально

дифференциальный

БРК – бортовой радио

комплекс

### 1 Аэродинамический облик ЛА

В ходе проектирования ЛА был внесен ряд изменений, затрагивающий общий вид ЛА.

Аэродинамическая схема и основные размеры крыла, хвостового оперения и управляющих

поверхностей не претерпели изменений. Общий вид разрабатываемого ЛА представлен на

рисунке 1.


Рисунок 1 – Общий вид ЛА

Приведем основные геометрические характеристики ЛА в таблицах 1 – 3

Таблица 1 – Геометрические характеристики крыла

A

8 | 0.750 | 1.678 | 0.210 | 0.236 | 0.352 | 1.8

Таблица 2 – Геометрические характеристики хвостового оперения

0.085 | 0.6 | 2 | 0.291 | 0.146 | 0.182 | 28

Таблица 3 – Характеристики управляющих поверхностей

Элероны | Руль высоты
Доля хорды ( ) | 0.3 | 0.3
Доля размаха ( ) | 0.5 | 0.8

Были внесены ряд изменений в конструкцию летательного аппарата, которые

отражены в таблице 4.

Таблица 4 – Основные изменения конструкции

Было | Стало
Профиль сечения фюзеляжа | Круговой | Эллиптический
Крепление хвостового оперения | Сопрягается с фюзеляжем | Хвостовая балка
Длина фюзеляжа | 1300 мм | 1350 мм (с учетом хвостовой балки)

Необходимость в внесенных изменениях в конструкцию обусловлена желанием

добиться положения центра масс аппарата в диапазоне допустимых центровок. Вид ЛА с

указанием центра масс представлен на рисунке 2.


Рисунок 2 – Положение центра масс ЛА

### 2 Аэродинамические характеристики

В предположении, что угловая скорость вращения мотора ограничена 7000 оборотами

в минуту, была построена кривая располагаемой тяги мотора от скорости воздушной

скорости ЛА. Как видно из анализа рисунка 3, ЛА может летать в широком диапазоне

скоростей с расчетной крейсерской 18 м/c.


Рисунок 3 – Зависимость располагаемой и требуемой тяги от воздушной скорости

Расчет динамических и статических аэродинамических характеристик был произведен

из анализа численных моделирований в прикладном пакете Ansys. Приведем результаты

моделирования на рисунках 4 – 6. Отметим, что расчет производился в связной системе

координат с летательным аппаратом (не успели перевести в скоростную ( ). Как видно из

анализа рисунков 4 – 6 зависимости коэффициентов моментов сил имеют отрицательный

наклон, что свидетельствует о статической устойчивости ЛА в продольном и поперечном

каналах. Хотя стоит изменить центровку на заднюю, чтобы добиться нулевого момента

тангажа (рисунок 4) при нулевом угле атаки.


Рисунок 4 – Статические аэродинамические коэффициенты в отсутствии отклонения управляющих поверхностей

Рисунок 5 - Статические аэродинамические коэффициенты при совместном отклонении рулей хвостового оперения


Рисунок 6 - Статические аэродинамические коэффициенты при совместном отклонении элеронов


Рисунок 7 – Главные динамические производные в зависимости от угла атаки

Как видно из анализа рисунка 7, все динамические производные отрицательны, что

говорит о динамической устойчивости ЛА.

### 3 Процесс изготовления ЛА

Для производства планера-прототипа команда планирует широко использовать

аддитивные технологии производства (3D печать FFF), а также композитные материалы

(фабричного | и | собственного | производства). | Силовой | каркас | БВС | состоит | из

воспринимающих основные нагрузки углепластиковых трубок (лонжерона крыла, трех

фюзеляжных и одной хвостовой балок) и «надетыми» на них шпангоутами, напечатанных из

угленаполненного пластика. Такой выбор обоснован высокими удельными механическими

характеристиками материалов и ожидаемыми нагрузками на силовой набор БВС:

изгибающими моментами, а в случае шпангоутов – также сжимающими напряжениями. Для

повышения жесткости и прочности шпангоутов на сжатие при печати будет использоваться

повышенное число слоев периметра для формирования соответствующих анизотропных

свойств детали. Обшивка фюзеляжа и прочие конструкционные элементы не являются несущими и печатаются из угленаполненного или обычного пластика. Крыло БВС, консоли

которого «надеваются» на упомянутый выше лонжерон, планируется изготавливать из

пенопласта на ЧПУ станке и укреплять стеклотканью, пропитанной эпоксидной смолой, с

направлением стеклонитей ±45° к лонжерону. Данный выбор обусловлен легкостью

обработки пенопласта, его низкой плотностью и способностью сформировать требуемый

профиль крыла. Стеклоткань же позволяет укрепить его поверхность и, благодаря выбранной

ориентации нитей, повысить жесткость и прочность крыла на скручивание.

Шпангоуты фиксируются на фюзеляжных трубках клеем. Крепление лонжерона

крыла, хвостовой балки и электродвигателя к главной фюзеляжной трубке осуществляется

через переходники, напечатанные из угленаполненного пластика, с помощью разъёмных

соединений. К полученному силовому каркасу прикручиваются все остальные детали.

Внутренние функциональные компоненты БВС укладываются и закрепляются на печатных

держателях, | располагаемых | между | шпангоутами. | Подробнее | конструкцию | можно

рассмотреть в электронном виде (файл Assembly.step).

Используемые материалы и связанные с ними оборудование и инструменты

приведены в таблице 5. Таблица составлена для планера БВС – функциональные элементы

БВС изготавливаются (покупаются) отдельно.

Таблица 5 – Используемые в производстве ЛА материалы, оборудование и инструменты

Материалы | Оборудование и инструменты
Углепластиковые трубки плетения 3K Plain диаметром 30, 16, 8 мм | Ножовка (обрезка по длине) Шуруповерт (сверление отверстий)
Угленаполненный филамент PETG-CF Eryone | 3D принтер Ghost 6

Филамент PETG REC Relax

Пенопласт XPS | ЧПУ станок-резчик
Стеклоткань 163 г/м2 Эпоксидная смола L Отвердитель EPH161 | Матрица из XPS собственного изготовления
ПВХ/пластиковые трубки диаметром 16, 8 мм | Ножовка (обрезка по длине)
Крепежные элементы (винты, гайки) | Отвертка, прямые руки
Клей эпоксидный 3M DP490 | Ручной аппликатор, кисть и прочее

При изготовлении шпангоутов используется 3D принтер Ghost 6 с диаметром сопла

0,6 мм. При подготовке деталей к печати настраивается высота слоев 0,2 мм.

Изготовление консоли крыла БВС выполняется в соответствии с следующим

разработанным технологическим процессом:

1. Подготовка пенопластовой заготовки – обрезка по длине;
2. Вырезание профиля крыла на ЧПУ станке с раскаленной струной. Движение каждого

из концов струны задается соответствующими профилями крыла БВС: корневой и

концевой. Таким образом создается трапециевидное крыло в соответствии с

спроектированным обликом БВС. Для выреза цилиндрических отверстий под

лонжерон крыла (диаметром 16 мм) и тяг управления элеронами (диаметром 8 мм)

струна разрезает пенопласт практически перпендикулярно его нижней кромке.

Примерная схема хода струны показана на рисунке .


Рисунок 8 - Примерная схема хода струны

3. Вырезанная консоль крыла извлекается из заготовки, а разрезы, сделанные струной

для выреза цилиндрических отверстий – заклеиваются. После выреза этих отверстий

остаются пенопластовые цилиндры – путем их обрезки по длине формируются

«заглушки», которые вставляются с внешней стороны крыла и фиксируются клеем.

4. Перед нанесением покрытия из стеклопластика, в цилиндрические отверстия

вставляются ПВХ или пластиковые трубки соответствующих диаметров. Это

необходимо для дальнейшего удержания формы и размера отверстий, т.к. в ином

случае они могут измениться после формирования композитного слоя.

5. Покрытие поверхности крыла стеклопластиком производится методом холодной

формовки в один слой. Как было упомянуто ранее, направление стеклонитей будет

составлять с лонжероном угол ±45°. Матрица изготавливается из XPS пенопласта с

помощью ЧПУ станка.

Хвостовое оперение изготавливается аналогично и закрепляется на хвостовой балке

через переходник из угленаполненного пластика.

Процесс сборки заключается в соединении деталей с помощью клея и резьбовых

соединений (было упомянуто ранее), в результате чего формируются следующие узлы БВС:

- фюзеляж – силовой каркас из трех углепластиковых трубок и шпангоутов, на которых

закреплены обшивка, держатели с внутренними элементами БВС, ВМГ и все

необходимые переходники;

- лонжерон крыла (углепластиковая трубка);
- две консоли крыла;
- хвостовая балка с V-образным оперением.

Таким образом, крупноузловая сборка БВС перед полетом заключается в

присоединении к фюзеляжу хвостовой балки (через переходник с фиксацией резьбовым

соединением), лонжерона крыла (через переходник) и «надеванием» консолей крыла на

лонжерон с их фиксацией. Помимо этого, соединяются тяги управляющих плоскостей с

сервоприводами в фюзеляже. БВС как в собранном, так и в разобранном виде сохраняет

возможность доступа к основным его функциональным элементам, в т.ч. для размещения

груза и судейского трекера.

### 4 Прочностные расчеты

Так как размеры управляющих поверхностей не были изменены, то вид центровочной

ведомости остался неизменным и представлен на рисунке 8.


Рисунок 9 – Центровочная ведомость

Максимальные положительная и отрицательная перегрузки равны | .

Согласно требованиям авиационных правил №25 была построена V-n диаграмма на рисунке

9, где отображены
, скорость сваливания, маневренная скорость, скорость

горизонтального полета ЛА и скорость пикирования соответственно. Также выделен участок

диаграммы, характеризующий перегрузки при совместном отклонении элеронов при запуске

с рук.


Рисунок 10 – V-n диаграмма

Для упомянутых ранее материалов в | таблице 5 | приведены их основные механические

характеристики. Так как в процессе изготовления широко используются аддитивные

технологии производства (3D печать FFF), то и анизотропные механические характеристики

таких деталей будут сильно зависеть от примененных параметров печати. Поэтому силами

команды был проведен натурный эксперимент по определению некоторых механических

характеристик образцов (рисунок 3), напечатанных из угленаполненного пластика PETG

сериями по 5 штук для двух случаев ориентации волокон пластика: вдоль длины образца (с

продольным заполнением) и поперек (с поперечным заполнением). Образцы закреплялись в

разрывной машине и подвергались нагрузке на растяжение со скоростью хода 10 мм/мин

вплоть до полного разрушения с записью данных о приложенной силе и деформации

образцов (рисунок 4). По полученным данным были оценены (как среднее по образцам)

модули упругости, пределы прочности и условные пределы текучести по направлениям вдоль

и поперек волокон печати (см. таблицу 2). Среднеквадратические отклонения для каждой

величины составили не более 4% от приведенных значений. Поскольку углеволокно не

связывает разные слои пластика друг с другом, свойства угленаполненного PETG по оси Z

сопоставимы с свойствами обычного PETG по оси Z.


Рисунок 11 – Пара разрушенных экспериментальных образцов с различной ориентацией волокон: поперечной (сверху) и продольной (снизу)

Информация о прочностных свойствах напечатанных из PETG образцов была

получена по протоколам испытаний [1–3] для пластика REC Relax, для стеклопластика – от

одного из производителей [4], данные об углепластике взяты из приведенных

производителем характеристик схожих по плетению и размерам трубок [5], при этом

свойства по оси Z были определены из параметров эпоксидных смол [6]. Свойства

пенопласта XPS взяты на основе [7]. Условный предел текучести , определяющий

напряжение, при котором остаточная относительная деформация достигает 0,2%, может быть

определен для используемых материалов по зависимости напряжения от относительной

деформации, полученной в ходе соответствующих испытаний. По протоколам [1–3] был

оценен условный предел текучести PETG при растяжении, при этом предел прочности при

сжатии не наблюдается в приведенных результатах. Данными об испытаниях других

материалов команда не обладает.

Таблица 6 – Перечень-ограничитель используемых конструкционных материалов

Материал | Направление | , ГПа | | , МПа | , МПа | , кг/м³
Углепластик | X(Y), растяж. | 55,8 | XY: 0,06 | – | 580 | 1500
| X(Y), сжатие | | | – | 633
| Z, растяж. | 3,1 | XZ/YZ: 0,35 | – | 72
| Z, сжатие | | | – | 140
PETG-CF | X, растяж. | 2,5 | 0,36 | 39,0 | 48,5 | 1260
| Y, растяж. | 1,9 | | 34,3 | 39,6
PETG | X(Y), растяж. | 1,12 | 0,38 | 27,6 | 36,5 | 1300

| Z, сжатие | 1,81 | | 51,7 | –
| Z, растяж. | 1,73 | | 25,9 | 33,6
XPS | растяж. | 0,02 | 0,39 | – | 0,6 | 30
| сжатие | | | – | 0,3
Стеклопластик | X(Y), сжатие | 20,6 | XY: 0,08 | – | 226,9 | 1750
| X(Y), растяж. | 17,2 | | – | 226,9
| Z, сжатие | 6,9 | XZ/YZ: 0,35 | – | 113,4
| Z, растяж. | 5,5 | | – | 51,6


Рисунок 12 – Необработанные данные зависимости приложенной силы от удлинения на примере серии испытаний образцов с продольной ориентацией волокон

Поверочный прочностной расчет был выполнен с использованием SOLIDWORKS

Simulation для крыла и хвостовой балки БВС. Команда уделила особое внимание заданию

анизотропных свойств материалов для проведения корректного моделирования.

Расчет прочности крыла был сведен к расчету прочности углепластикового

лонжерона. Пусть пенопласт и обладает существенно более низким пределом прочности по

сравнению с углепластиком, высокая жесткость последнего не позволит достичь его раньше

момента разрушения лонжерона. Расчетная схема представлена на рисунке 5. Расчет

производился для половины лонжерона (одной консоли крыла), на часть трубки

накладывалось граничное условие «зафиксированная геометрия», что соответствует

заходящему в переходник сегменту трубки. На остальную часть трубки (цилиндрическую поверхность) была наложена распределенная нагрузка, соответствующая формируемой одной

консолью крыла подъемной силе при максимальной расчетной перегрузке

(определено из V-n диаграммы):

В силу симметрии трубки рассмотрение отрицательной перегрузки не имеет смысла,

т.к. | .


Рисунок 13 – Расчетная схема лонжерона консоли крыла, вид сбоку

На | рисунке | 6 показаны эпюра напряжений по Мизесу и эпюра эквивалентных

деформаций, построенные по линии, проходящей вдоль трубки по верхней её части.

Концевая часть лонжерона при моделировании переместилась на чуть более чем 7 мм

вследствие приложенной нагрузки.


Рисунок 14 – Эпюры напряжений и эквивалентных деформаций лонжерона

В ходе моделирования был определен минимальный запас прочности лонжерона

крыла, равный 7,7. Данное значение позволяет заявить о выполнении условия прочности для

конструкции | крыла (в | соответствии | с | [АП25]), несмотря на некоторую | долю

неопределенности в истинных характеристиках композита, зависящих от множества

факторов. Наиболее нагруженные участки лонжерона (с наименьшим запасом прочности)

можно увидеть на рисунке 14.


Рисунок 15 – Эпюра запаса прочности лонжерона консоли крыла

Для проведения статического анализа хвостовой балки БВС была рассчитана

аэродинамическая сила, создаваемая хвостовым оперением при максимальном отклонении

управляющих поверхностей при различном угле атаки (рисунок | 8). Расчетная схема для
хвостовой балки приведена на | рисунке | 9. Как и в случае с лонжероном, моделирование было

сведено к рассмотрению углепластиковой трубки. На участок трубки, соответствующий

расположению оперения, накладывалась распределенная внешняя сила | . На | рисунке

10 показаны эпюра напряжений по Мизесу и эпюра эквивалентных деформаций, построенные

по линии, проходящей вдоль трубки по верхней её части. Концевая часть хвостовой балки

при моделировании переместилась на чуть более чем 6 мм вследствие приложенной

нагрузки.


Рисунок 16 – График создаваемой хвостовым оперением аэродинамической силы от угла атаки

Рисунок 17 – Расчетная схема хвостовой балки, вид сбоку

Рисунок 18 – Эпюры напряжений и эквивалентных деформаций хвостовой балки

В ходе моделирования был определен минимальный запас прочности хвостовой балки,

равный 26, что позволяет заявить о выполнении условия прочности. Наиболее нагруженные

участки (с наименьшим запасом прочности) можно увидеть на рисунке 11. По результатам

моделирования можно считать, что хвостовая балка БВС является особо надежным

элементом силового каркаса БВС.

Рисунок 19 – Эпюра запаса прочности хвостовой балки

### 5 Бортовое оборудование

### 5.1 Состав бортового оборудования

Используемое бортовое оборудование и номинальные мощности представлены в

таблице 4

Таблица 7 – Состав бортового оборудования

ПК H743-WING V3 | Mateksys ELRS | GPS M10Q-5883 | ПВД ASPD-4525 | Ebyte E32-433T30D | FPV камера с передатчи ком | Сервопри вод PDI-HV2006M G
0.8 Вт | 0.375 Вт | 0.065 Вт | 0.025 Вт | 3 Вт | 0.2 Вт | 10 Вт

Структурная схема БО представлена рисунке 9


Рисунок 20 – Структурная схема бортового оборудования

### 5.2 Система питания

Согласно расчетам СУ суммарная потребляемая мощность ЛА в горизонтальном

полете составила | . Для того чтобы находиться воздухе в течение

, необходима энергия с запасом в 10% равная:

Таким образом, сборка 4S2P из Li-ion батарей Molicel типоразмера 18650 c

характеристиками, представленными в таблице 8, являются подходящими для системы

питания ЛА.

Таблица 8 - Характеристики системы питания ЛА

Емкость ячейки, | Номинальное напряжение, В | Масса ячейки, г | Удельная энергия сборки,
2.8 | 3.7 | 50 | 185

Тогда расчетное время полета равно

### 5.3 Оценка безопасности эксплуатации БО

В таблице 9 представлены степени критичности выхода из строя того или иного

элемента бортового оборудования. Последствия выхода из строя подсистемы, действия

команды в случае отказа той или иной подсистемы.

Таблица 9 - степени критичности выхода из строя того или иного элемента бортового

оборудования. Последствия выхода из строя подсистемы, действия команды в случае

отказа той или иной подсистемы

Тип БО | Степень критичности | Последствия | Действия команды
Полетный контроллер | Критичн о | Неконтролиру емое падение | Отход от позиций возможного падения
Регулятор оборотов, мотор | Критичн о | Отсутствие тяги | Переход на ручное управление и обеспечение плавного спуска БВС за счет управляющих поверхностей
Сервопривод ы | Критичн о | Отсутствие маневренности | Переход на ручное управление и обеспечение плавного спуска БВС за счет мотора

Радиоприем ник телекоманд | Критичн о | Отсутствие связи с БВС | Возвращение БВС на точку старта в автоматическом режиме
Радиопереда тчик телеметрии | Средняя степень критичности | Отсутствие данных о состоянии БВС | Сохранение телеметрии на память БВС
Камера FPV, передатчик видео потока | Средняя степень критичности | Отсутствие видео потока | Визуальное сопровождение
Датчик воздушной скорости | Средняя степень критичности | Отсутствие данных о скорости потока | Переход на ручное управление
GPS, компас | Средняя степень критичности | Отсутствие данных положения БВС | Переход на ручное управление

Вероятность отказа всех систем уменьшается за счет использования надежных

способов коммутации (пайка и клеммы) датчиков и управляющих элементов с полетным

контроллеров, а также за счет обеспечения стабильного питания от аккумуляторных батарей.

### 5.4 Разрабатываемые аппаратная и программная части

Полетный контроллер решает задачи сбора информации с датчиков расположенных на

борту БПЛА, обработки принятых данных и выдачу управляющих воздействий. Полетный

контроллер представляет из себя стек из двух печатных плат, одна плата отвечает за

коммутацию питания, вторая выполняет основные задачи полетного контроллера.

Фотография полетного контроллера представлена на рисунке 20.


Рисунок 21 – Вид полетного контроллера


Рисунок 22 – Вид трассировки плат питания и контроллера

Плата коммутации питания преобразует напряжение с батареи 12-24В в 5В и 3.3В,

необходимых для работы периферийных устройств внутренних датчиков и основного

вычислителя.

На второй плате расположен микроконтроллер STM32F405RGTx и 9-ти освой модуль

акселерометр, гироскоп, магнитометр MPU9250, связь модуля с микроконтроллером

реализована по интерфейсу SPI. Остальные модули, представленные на структурно-

функциональной схеме (см. приложение «структурная схема полетного контроллера.pdf»),

являются внешними и подключается шлейфами и кабельными сборками в разъемы,

расположенные на печатных платах. К внешним модулям относятся ГНСС-(NEOWAY G7A,

связывается с МК по интерфейсу UART), ПВД (MATEKSYS ASPD-4525 связывается с МК

по интерфейсу I2C), КТРЛ (E32-433T30D – LoRa SX1278, командно-телеметрическая радио

линия, UART), барометр BMP280 (I2C), flash память CJMCU-2516 для сохранения информации с датчиков на борту (интерфейс SPI), приемник команд управления полетом

(Mateksys ELRS 2,4 ГГц, I2C). Четыре канала таймеров используются в режиме ШИМ

модуляции для установки положения управляющих рулей, посредством управления

сервоприводами PDI-HV2006MG CORELESS, для работы с основным двигателем через

контроллер оборотов Skywalker 60A, активации системы спасения и выбрасывания груза

(реализовано с помощью сервопривода PDI-HV2006MG CORELESS).

Конфигурация полетного контроллера происходит с компьютера с помощью

написаного ПО на Qt, изображение интерфейса представлено на рисунке 21 через КТРЛ, либо

по протоколу UART через специальный шлейф.


Рисунок 23 - Интерфейс взаимодействия с полетным контроллером

### 5.5 Описание работы встроенного программного обеспечения

Работа ВПО БПЛА разбита на несколько этапов:

- калибровка
- загрузка предполетного задания
- предполет
- готовность
- взлет
- полет по заданию
- выброс полезной нагрузки
- активация системы спасения
- поиск

Калибровка:

В данном режиме происходит калибровка бортовой БИНС БПЛА.

Загрузка полетного задания:

В режиме загрузки полетного задания в настройки БВМ загружаются такие

параметры, как:

- Точки маршрута для пролета
- Точки для выброса полезной нагрузки
- Другие характеристики полета

Предполет:

В режиме «предполет» все бортовые системы БПЛА находятся в спящем режиме, при

котором потребление ими энергии либо отсутствует вовсе, либо минимально. В данном

режиме БПЛА может поддерживать готовность реализовать полетную миссию в течении

пяти часов.

Готовность:

В режиме готовности активируются бортовые системы самолета, они находятся в

ожидании команды от БВМ о начале выполнения полетного задания.

Взлет:

Перед запуском БПЛА, на него по радиоканалу подается команда перехода в режим

взлет, что активирует систему ориентации и стабилизации и систему регулирования тяги.

БВМ по внутренней синхронизации считывает данные со всех измерительных модулей

таких как БИНС, ГНСС, ПВД, барометр, делает необходимую цифровую обработку,

фильтрацию и отправляет команды блокам управляющим полетом, блоку ориентации и

стабилизации и регулирования тяги.

Полет:

При переходе в этот режим БВМ принимает решение о изменении траектории

движения, в зависимости от заданной траектории полета в полетном задании. Управляющее

воздействие на рули поворота создается исходя из показаний БИНС и ГНСС, математически

в ВПО данная петля обратной связи реализована через ПИД регулятор. В момент подлета к

точке выброса полезной нагрузки на заданном расстоянии БВМ принимает решение о

переходе в режим «выброс полезной нагрузки».

Выброс полезной нагрузки:

В режиме выброса полезной нагрузки активируется система сброса полезной нагрузки.

Система дает управляющее воздействие и происходит открытие дверц блока полезной нагрузки. После освобождения полезной нагрузки дверцы механически приходят в исходное

положение.

Активация системы спасения:

В режиме «активация системы спасения», головной обтекатель откидывается и

фиксируется с наружной части корпуса БПЛА, вытягивая за собой парашют. С помощью

показаний с датчика освещенности фиксируется момент времени выброса парашюта и

отправляется через БРК в ЦУП.

Поиск:

После приземления ВПО переходит в режим «поиск», при этом активируется свето-

звуковой сигнал, для обнаружения места приземления БПЛА.

### 6 График работ

График работ прилагается по ссылке (https://disk.yandex.ru/d/HnMQzW_9t9-L6A)

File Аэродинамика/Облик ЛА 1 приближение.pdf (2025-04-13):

Для оценки площади хвостового оперения воспользуемся методом объёмных коэффициентов ([1] стр 158-161). В нашем случае хвостовое оперение имеет тип V-tail, поэтому под горизонтальным(HT) и вертикальным(VT) хвостовым оперением будем понимать проекции V-tail на горизонтальную и вертикальную плоскости соответственно.

Введем обозначения :
LVT - плечо момента рыскания, создаваемого вертикальным оперением
LHT - плечо момента тангажа, создаваемого горизонтальным оперением SVT , SHT - площади вертикального и горизонтального оперений
SW - проекционная площадь крыла
bW - размах крыла
CW - средняя хорда крыла
сVT , cHT - объёмные коэффициенты вертикального и горизонтального оперений CVT ,C HT - средние хорды вертикального и горизонтального оперений
bVT ,bHT - размахи вертикального и горизонтального оперений
1) согласно ([1], стр 160, table 6.4, sailplane) примем c HT=0.5 ,cVT=0.04.
2) оценим LVT, LHT:
В нашем случае LVT=LHT=L
Длина фюзеляжа, вмещающего только основные электронные компоненты и один груз в предложенной компоновке, составляет не менее 700 мм. Пусть полная длина фюзеляжа есть 700+l мм. Тогда по ([1], стр 160) оценим L≈0.6(700+l) . С другой стороны L=l+0.35. Таким образом из 0.6(700+l)≈L≈l+350 ⇒ l≈175 мм и L≈525 мм.
3) SW ≈0.366 м

2
, bW =1.6 м, CW ≈230 мм.
4) тогда по ([1], стр 159, формулы (6.28-6.29) )

SVT=

cVT bW SW

LVT

≈0.022 м

2
, SHT=

cHT CW SW

LHT

≈0.080 м

2
5) Примем удлинения вертикального и горизонтального оперений AR=3.

SHT=C HT⋅bHT , AR=

bHT

2

SHT

⇒ C HT bHT=

bHT

2
AR

,bHT=C HT AR , SHT=C HT

2

AR ⇒ C HT=√
SHT
AR

≈0.163 м

аналогично CVT≈0.086 м

6) bHT=

SHT

C HT

≈0.497 м, bVT=

1
2

SVT

CVT

=0.128 м т. к. лопатки смотрят только вверх

Используя полученные характеристики горизонтального и вертикального оперений как проекций V-tail, рассчитаем его собственные характеристики

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

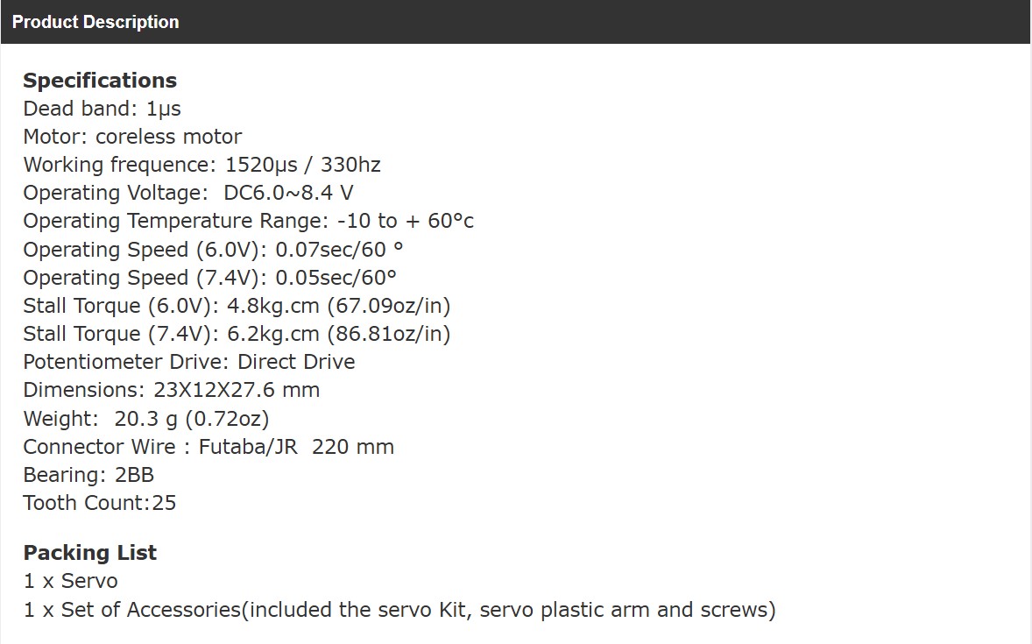
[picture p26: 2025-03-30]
БортовоеОборудование/ДокументацияНаЭлементыБО/Сервоприводы/ServoSpecification.jpg

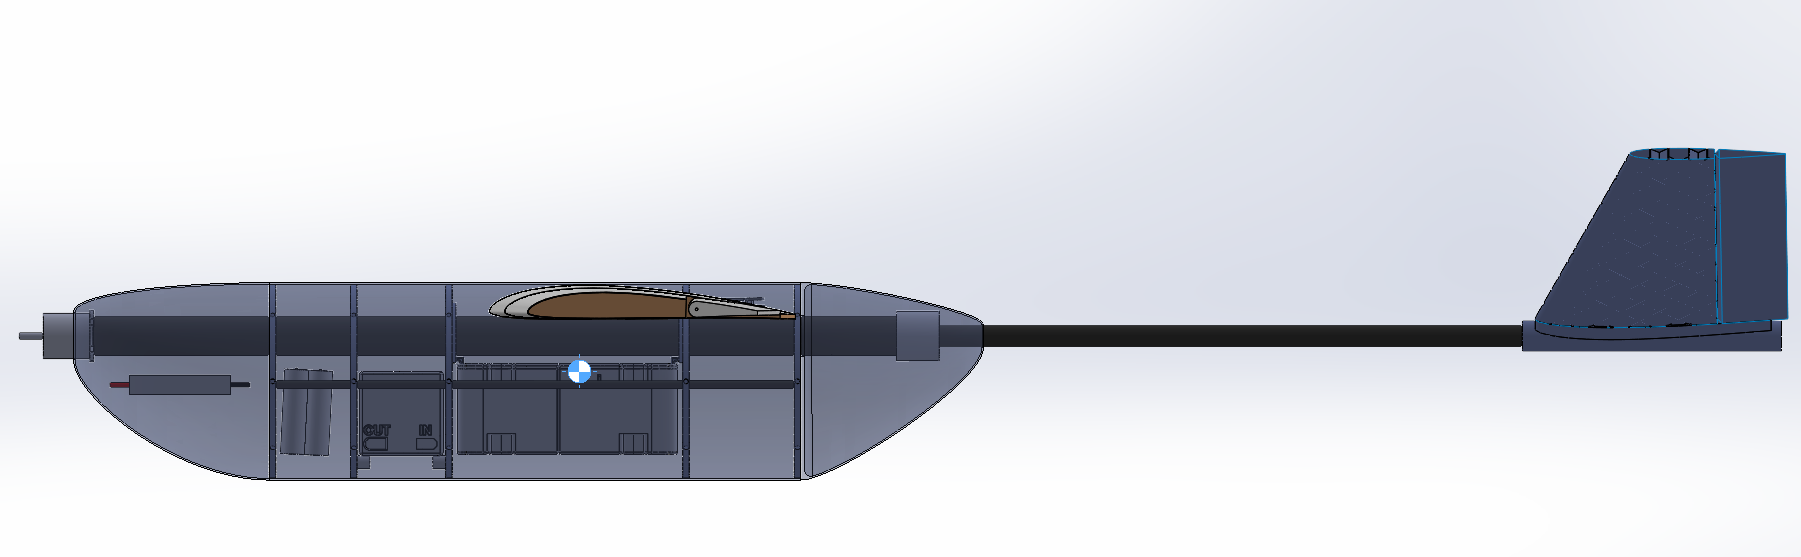
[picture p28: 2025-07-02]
ПроизводственныйОтчет/SideView.png

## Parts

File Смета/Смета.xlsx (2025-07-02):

Смета
№, п/п | Наименование материалов | продавец | ед. изм. | кол-во | стоимость | сумма
Винтомоторная группа и электропитание
1 | Мотор Sunnysky X2814 | ali (https://aliexpress.ru/item/4001138655063.html?sku_id=10000014777141872) | шт | 1 | 3502 | 3502 ₽
2 | Воздушный винт 11х8 | ali (https://aliexpress.ru/item/4001225006526.html?sku_id=10000015357939200) | шт | 1 | 1349 | 1349 ₽
3 | Регулятор оборотов Skywalker 60A V2 | ali (https://aliexpress.ru/item/1005004262445780.html?sku_id=12000037181002937) | шт | 1 | 2409 | 2409 ₽
4 | Скоба винта | ali (https://aliexpress.ru/item/4001225006526.html?sku_id=12000028994119936) | шт | 1 | 960 | 960 ₽
5 | Аккумуляторы Molicel 18650 | ozon (https://www.ozon.ru/product/akkumulyator-18650-litiy-ionnyy-li-ion-nizkotemperaturnyy-3-6v-molicel-inr-18650-p28a-2800mach-1-sht-704527024/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) | шт | 8 | 1100 | 8800 ₽
Материалы планера БВС
6 | Карбоновая трубка 30х28х1000мм | ozon (https://www.ozon.ru/product/karbonovaya-trubka-30-28-1000mm-918601149/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) | шт | 1 | 2102 | 2102 ₽
7 | Карбоновая трубка 16х14х1000мм | ozon (https://www.ozon.ru/product/karbonovaya-trubka-16-14-1000mm-866834872/?_bctx=CAQQq7gs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) | шт | 2 | 1108 | 2216 ₽
8 | Карбоновые трубки 2 шт 8х4х500мм | ozon (https://www.ozon.ru/product/2-sht-karbon-trubka-8-4-500-glyantsevyy-odnotonnyy-1882000551/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) | шт | 1 | 1356 | 1356 ₽
9 | PETG-CF Eryone 1,75 мм, 1 кг | ozon (https://www.ozon.ru/product/plastik-carbon-fiber-petg-eryone-1-75-mm-1kg-zelenyy-green-petg-cf-uglenapolnennyy-filament-dlya-2064500423/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) | шт | 1 | 1838 | 1838 ₽
10 | PETG REC Relax 1,75 мм, 0,75 кг | ozon (https://www.ozon.ru/product/katushka-plastika-rec-relax-petg-1-75mm-0-75-kg-prozrachnaya-1421535891/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) | шт | 1 | 1569 | 1569 ₽
11 | Технониколь XPS Carbon Eco 100 мм, 1 уп. | ozon (https://www.ozon.ru/product/tehnonikol-xps-carbon-eco-100-mm-1-up-2-74-m2-4-plity-uteplitel-iz-penopolistirola-dlya-sten-1856676313/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) | шт | 1 | 3387 | 3387 ₽
12 | 200 гр. эпоксидная смола L + 50 гр. отвердитель EPH 161 | graphit-pro (https://graphite-pro.ru/catalog/epoxy-resins/эпоксидная-смола-l-отвердитель-eph-161-90-мин/) | шт | 1 | 1319 | 1319 ₽
13 | Стеклоткань 163 г /м², 1 м² | graphite-pro (https://graphite-pro.ru/term/term/стеклоткань-163-г-м-²-твилл-ширина-100-см/) | шт | 1 | 729 | 729 ₽
14 | Клей эпоксидный 3М DP490, 50 мл | vseinstrumenti (https://www.vseinstrumenti.ru/product/klej-dvuhkomponentnyj-epoksidnyj-3m-chernyj-kartridzh-50-ml-dp490-16189655/) | шт | 1 | 4800 | 4800 ₽
15 | ПВХ трубка, 16 мм | vseinstrumenti (https://www.vseinstrumenti.ru/product/zhestkaya-truba-promrukav-pvh-3-h-metrovaya-tyazhelaya-d16-pr-0416-1272216/) | шт | 1 | 210 | 210 ₽
16 | Пластиковые трубки, 8 мм | ali (https://aliexpress.ru/item/1005006277502978.html?sku_id=12000036578735428) | шт | 1 | 250 | 250 ₽
17 |  |  |  |  |  | 0 ₽
18 |  |  |  |  |  | 0 ₽
19 |  |  |  |  |  | 0 ₽
20 |  |  |  |  |  | 0 ₽
21 |  |  |  |  |  | 0 ₽
Итог |  |  |  |  |  | 36796 ₽

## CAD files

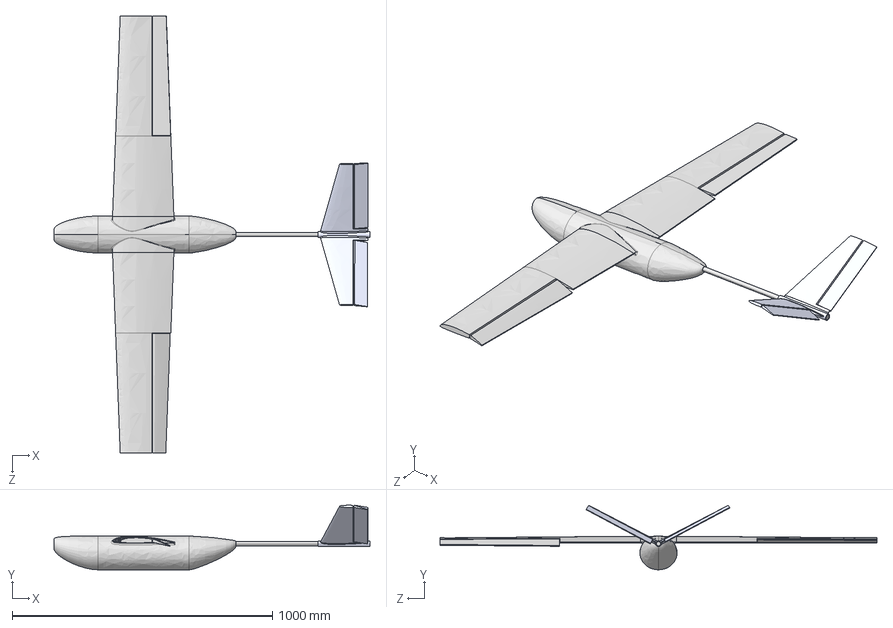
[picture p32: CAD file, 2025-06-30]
Модель/CFD/AssemblyCFD.STEP
1215.0 x 248.3 x 1680.0 mm
FuselageCFD
ÝëåðîíËåâûé
蓦屦铐橡噔
唒錪 x 2
Õâîñò x 2
扻臇樏襜襌碭嚦觜FD
署钏邂铄CFD
署钕疣忸錍FD

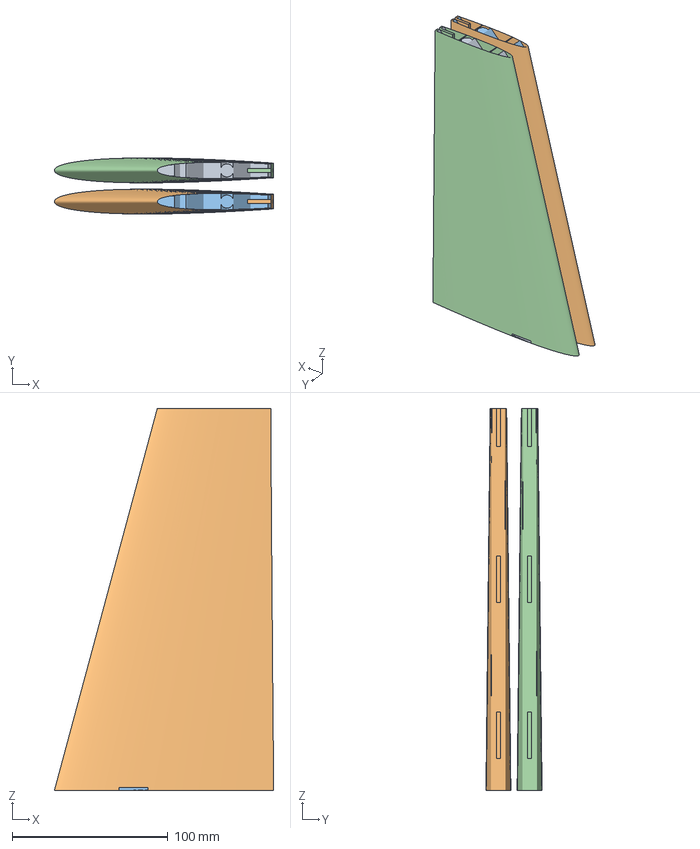
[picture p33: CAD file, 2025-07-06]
Модель/Model2021/Tail2021/STL/MainGrid.3mf
140.6 x 36.0 x 245.0 mm
MainGrid.STL x 2
MainSurface.STL x 2

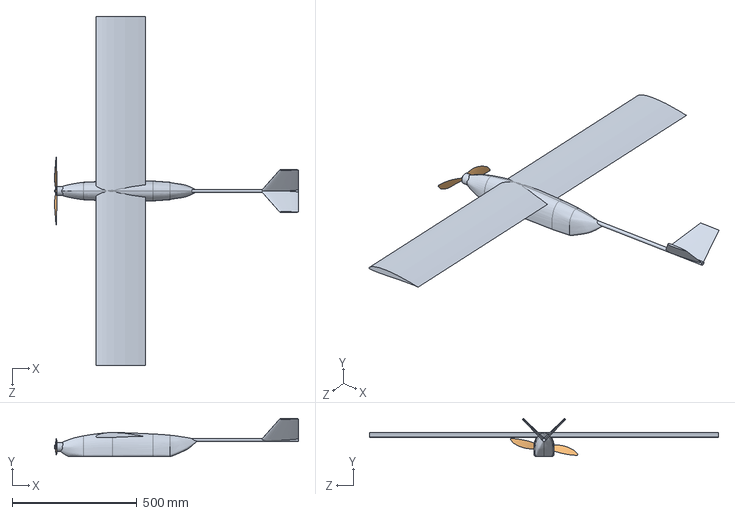
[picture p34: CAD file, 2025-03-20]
КонцептуальныйДизайн/Модель/Assembly.SLDASM
978.8 x 154.0 x 1400.0 mm
ConceptPlane
11x4.7_pusher_9mm.step

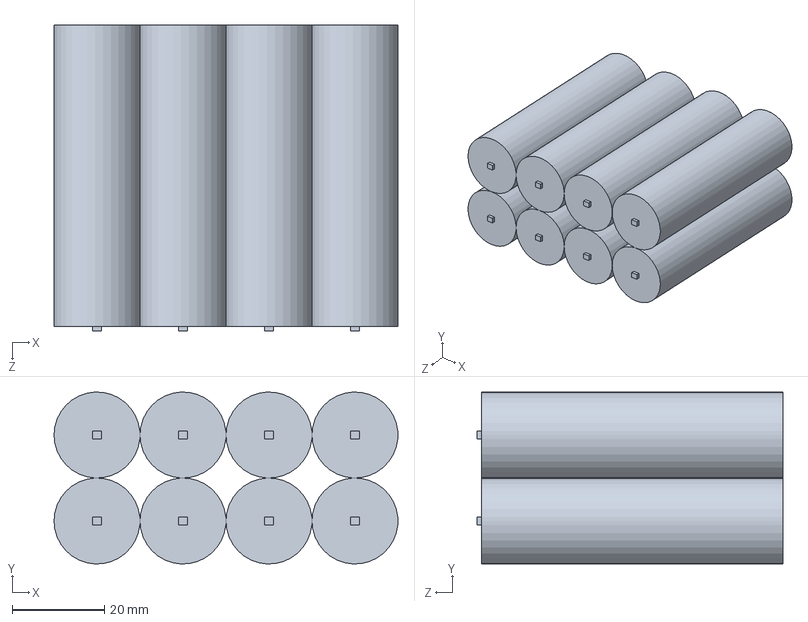
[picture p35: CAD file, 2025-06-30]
Модель/Model2021/Battery2021/2p4s18650.SLDASM
74.4 x 37.2 x 66.2 mm
Аккумулятор18650 x 8

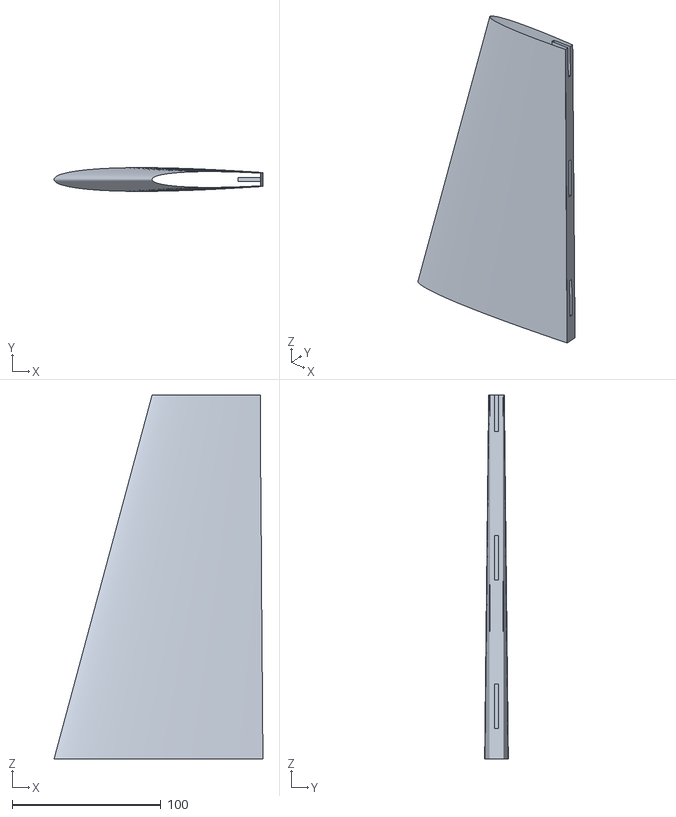
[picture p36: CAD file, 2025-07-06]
Модель/Model2021/Tail2021/STL/MainSurface.STL
140.6 x 16.0 x 245.0

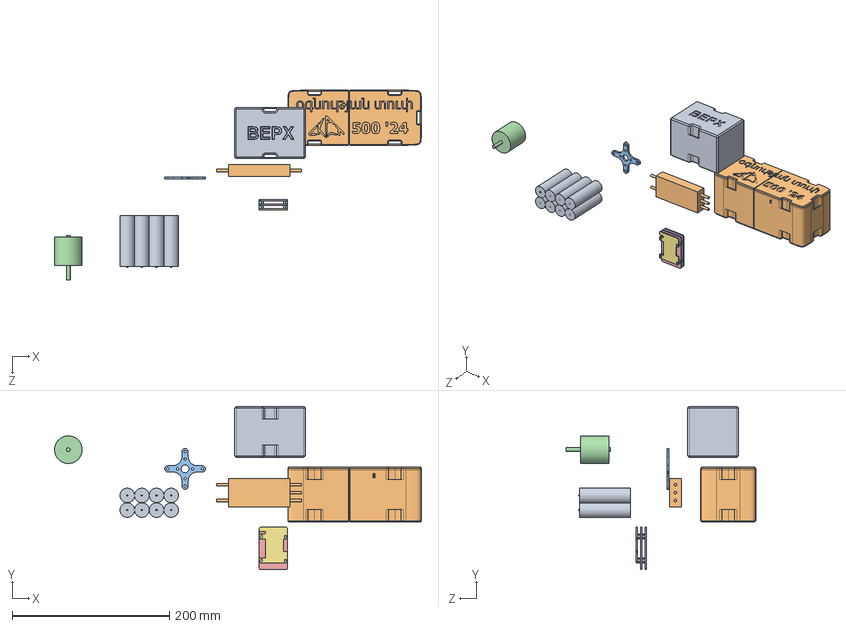
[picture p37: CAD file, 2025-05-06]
Модель/NewModel/AssemblyNew.SLDASM
466.5 x 207.7 x 241.0 mm
Аккумулятор18650 x 8
ESC
MotorMount
МоторAT2814
FCBoard1
FCBoard2
FCBoard3
PCBHolder x 8
tracker_v2025.step
500_g_payload.step

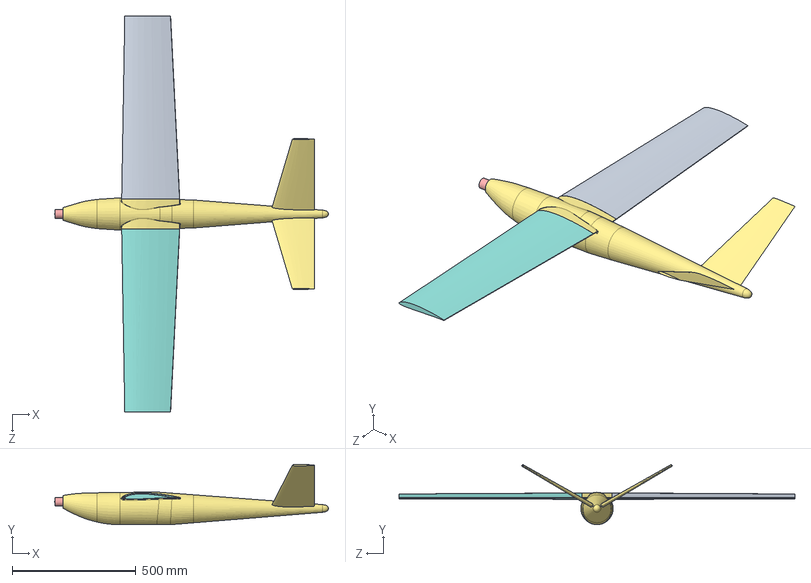
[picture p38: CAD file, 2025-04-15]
Модель/NewModel/Assembly.SLDASM
1107.7 x 244.1 x 1600.0 mm
ESC
Груз
Аккумулятор18650 x 8
tracker_v2024.step
МоторAT2814
MotorMount
Fuselage
WingLeft
WingR

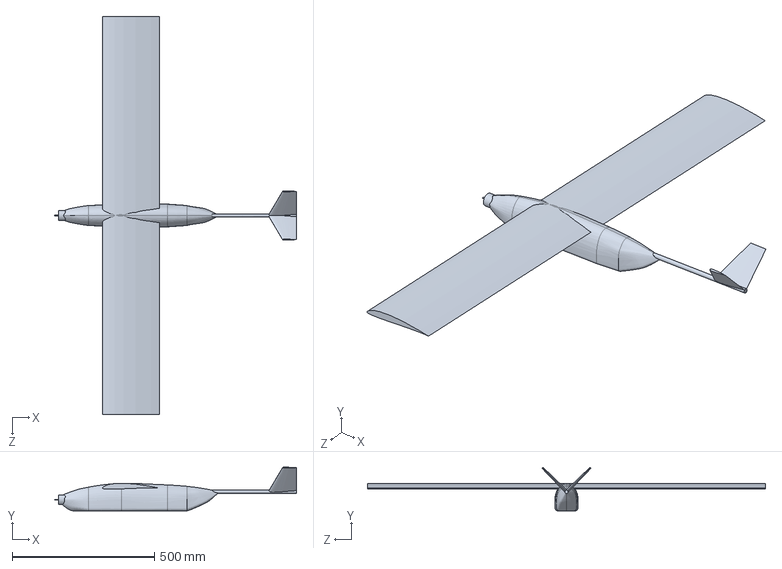
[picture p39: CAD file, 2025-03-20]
КонцептуальныйДизайн/Модель/ConceptPlane.SLDPRT
853.0 x 153.8 x 1400.0 mm

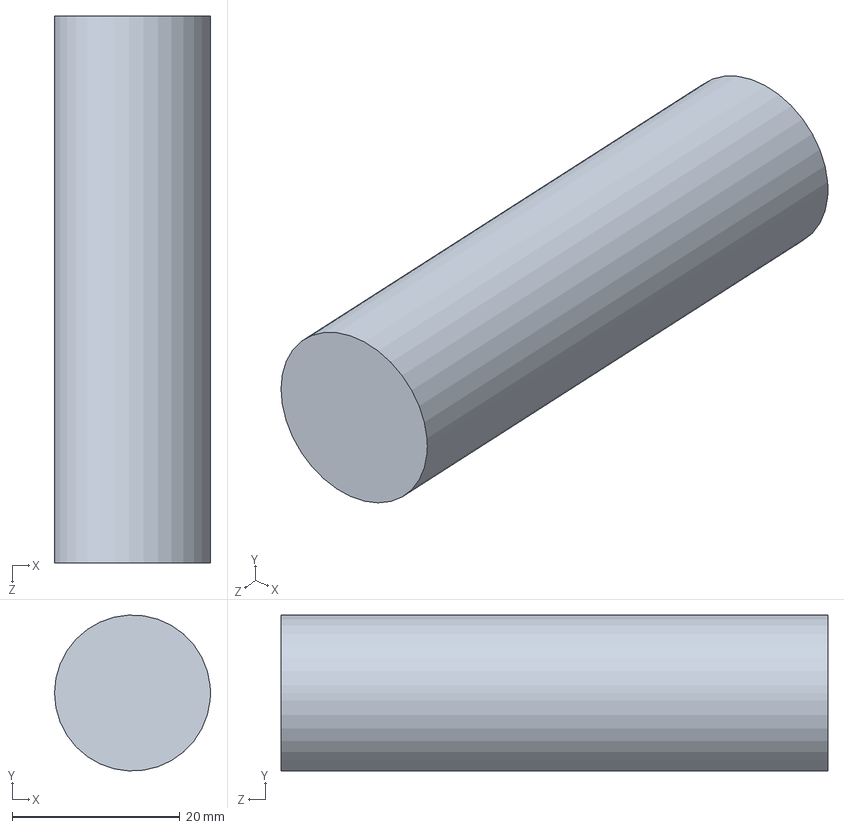
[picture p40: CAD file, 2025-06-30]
Модель/Model2021/Battery2021/Аккумулятор18650.SLDPRT
18.6 x 18.6 x 65.2 mm

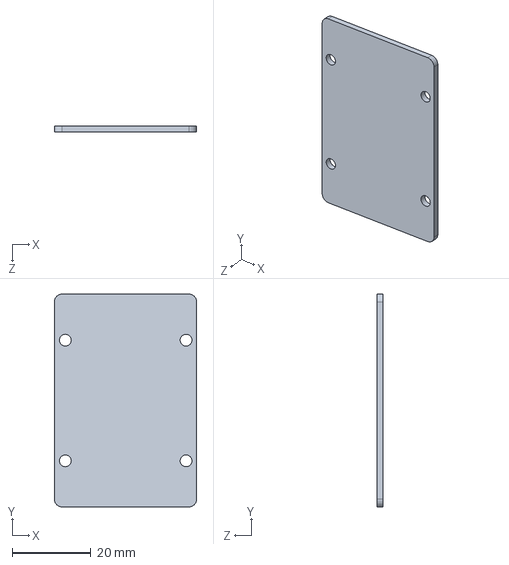
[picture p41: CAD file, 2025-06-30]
Модель/Model2021/FlightController2021/FCBoard1.SLDPRT
36.1 x 54.0 x 1.60 mm

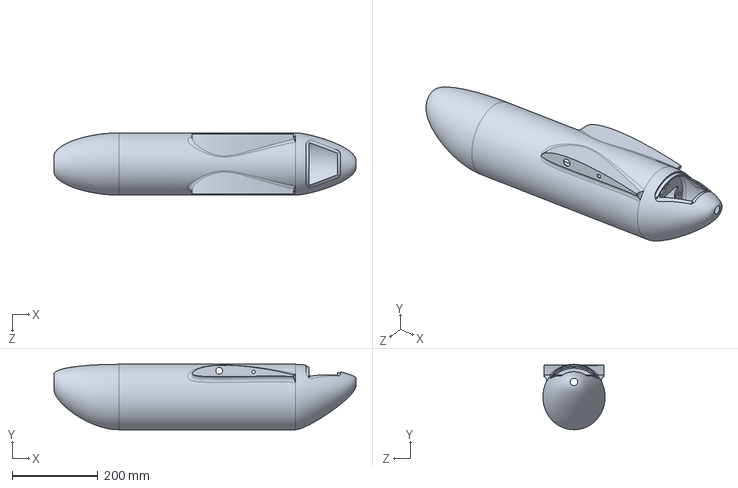
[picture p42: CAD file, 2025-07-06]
Модель/Model2021/Fuselage2021/Fuselage.SLDPRT
702.4 x 152.4 x 144.9 mm

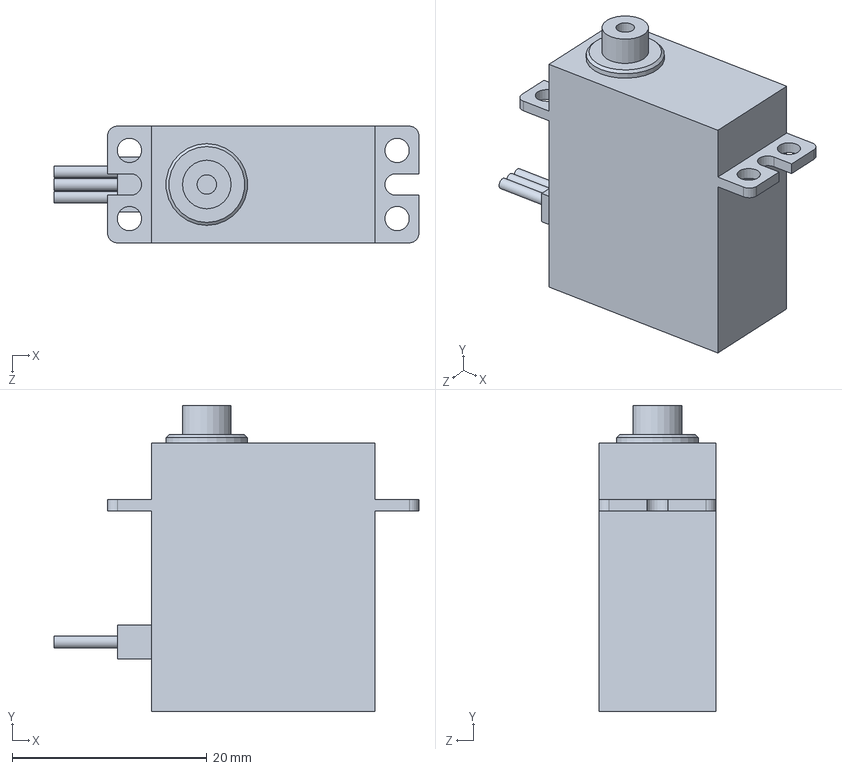
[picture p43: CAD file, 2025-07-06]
Модель/Model2021/JXServo.SLDPRT
37.5 x 31.5 x 12.0 mm

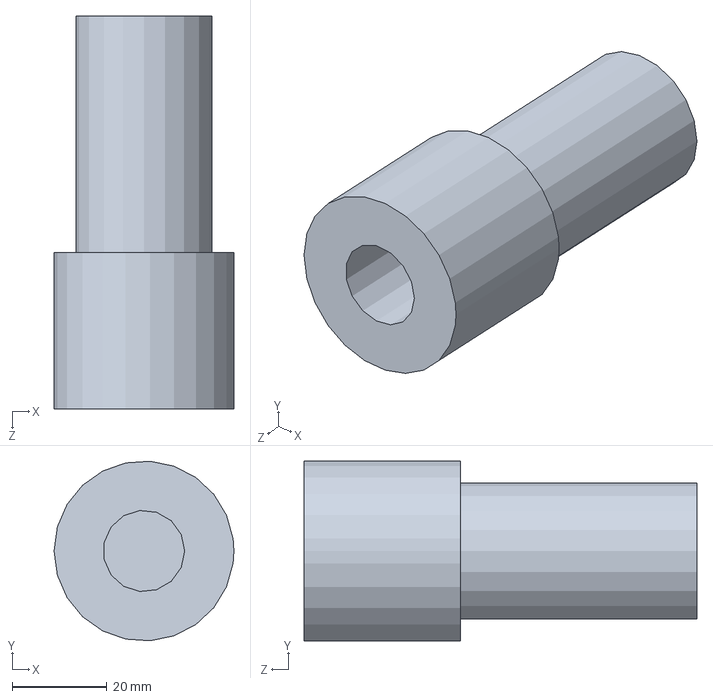
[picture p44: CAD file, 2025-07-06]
Модель/Model2021/Tail2021/ПереходникХвоста.SLDPRT
38.0 x 37.9 x 83.0 mm

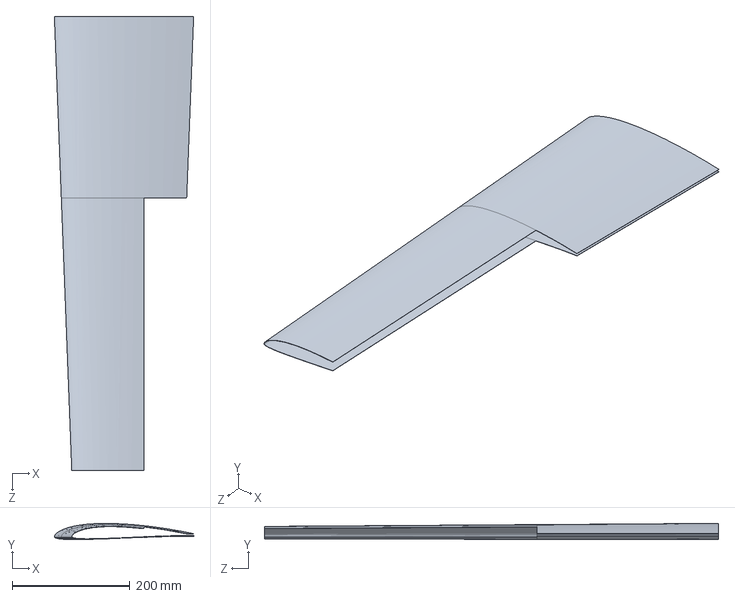
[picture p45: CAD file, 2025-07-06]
Модель/Model2021/Wing2021/ОболочкаКрылаЛевого.SLDPRT
236.3 x 27.5 x 770.0 mm

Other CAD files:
Модель/NewModel/2p4s18650.SLDASM
Модель/NewModel/PCBHolder.SLDPRT
Модель/CFD/КоннекторХвостаCFD.SLDPRT
Модель/Model2021/FlightController2021/FCBoard3.SLDPRT
КонцептуальныйДизайн/Модель/Assembly.SLDDRW
КонцептуальныйДизайн/Модель/propeller.STEP
Модель/CFD/AssemblyCFD.SLDASM
Модель/CFD/FuselageCFD.SLDPRT
Модель/CFD/КрылоЛевоеCFD.SLDPRT
Модель/CFD/КрылоПравоеCFD.SLDPRT
Модель/Model2021/ESC.SLDPRT
Модель/Model2021/FlightController2021/FCBoard2.SLDPRT
Модель/Model2021/FlightController2021/FCSketch.SLDPRT
Модель/Model2021/FlightController2021/ПолетныйКонтроллер.SLDASM
Модель/Model2021/FlightController2021/ПолетныйКонтроллер.STEP
Модель/Model2021/Fuselage2021/Fuselage-Поверхность-По сечениям1.SLDPRT
Модель/Model2021/Fuselage2021/Fuselage-Поверхность-По сечениям2.SLDPRT
Модель/Model2021/Fuselage2021/Fuselage-Поверхность-По сечениям3.SLDPRT
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

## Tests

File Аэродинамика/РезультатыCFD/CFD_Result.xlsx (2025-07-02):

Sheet: Основной
Name | P2 - Va | P3 - Alpha | P4 - Beta | P5 - NoMI | P6 - PoP | P14 - A10@DS_eler_prav@Угол1@AssemblyCFD.Assembly | P15 - A10@DS_rul_visoti@Угол2@AssemblyCFD.Assembly | P1 - Mesh Elements | P7 - Fx | P8 - Fy | P9 - Fz | P10 - Mx | P11 - My | P12 - Mz | P13 - Current Time Step | Fx | Fy | Cy | cx | mz
Units | m s^-1 | degree | degree |  |  |  |  |  | N | N | N | J | J | J |  | -2.253613721 | -4.377287468 | -0.06230898885 | -0.03207931698 | 0.1089173403
DP 0 (Current) | 18 | -4 | 0 | 20 | 0.05 | 90 | 90 | 11381566 | -1.94294 | -4.52376 | 0.0141065 | 0.0123695 | 0.00841698 | 1.59333 | 51 | -2.226839337 | 7.350129152 | 0.1046262368 | -0.03169819401 | 0.004338038629
DP 1 | 18 | -2 | 0 | 20 | 0.05 | 90 | 90 | 11381566 | -2.48187 | 7.26798 | 0.0110231 | 0.0135601 | 0.00634767 | 0.0634603 | 51 | -2.43891 | 19.1948 | 0.273230531 | -0.03471693762 | -0.09758968531 | S | 0.354
DP 2 | 18 | 0 | 0 | 20 | 0.05 | 90 | 90 | 11381566 | -2.43891 | 19.1948 | 0.00690811 | 0.0114212 | 0.00345306 | -1.42762 | 51 | -2.868234434 | 31.08006473 | 0.4424126633 | -0.04082820438 | -0.1994292065 | v | 18
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

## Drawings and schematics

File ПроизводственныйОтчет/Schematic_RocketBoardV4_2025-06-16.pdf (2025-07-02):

## Power distribution

## PowerLed

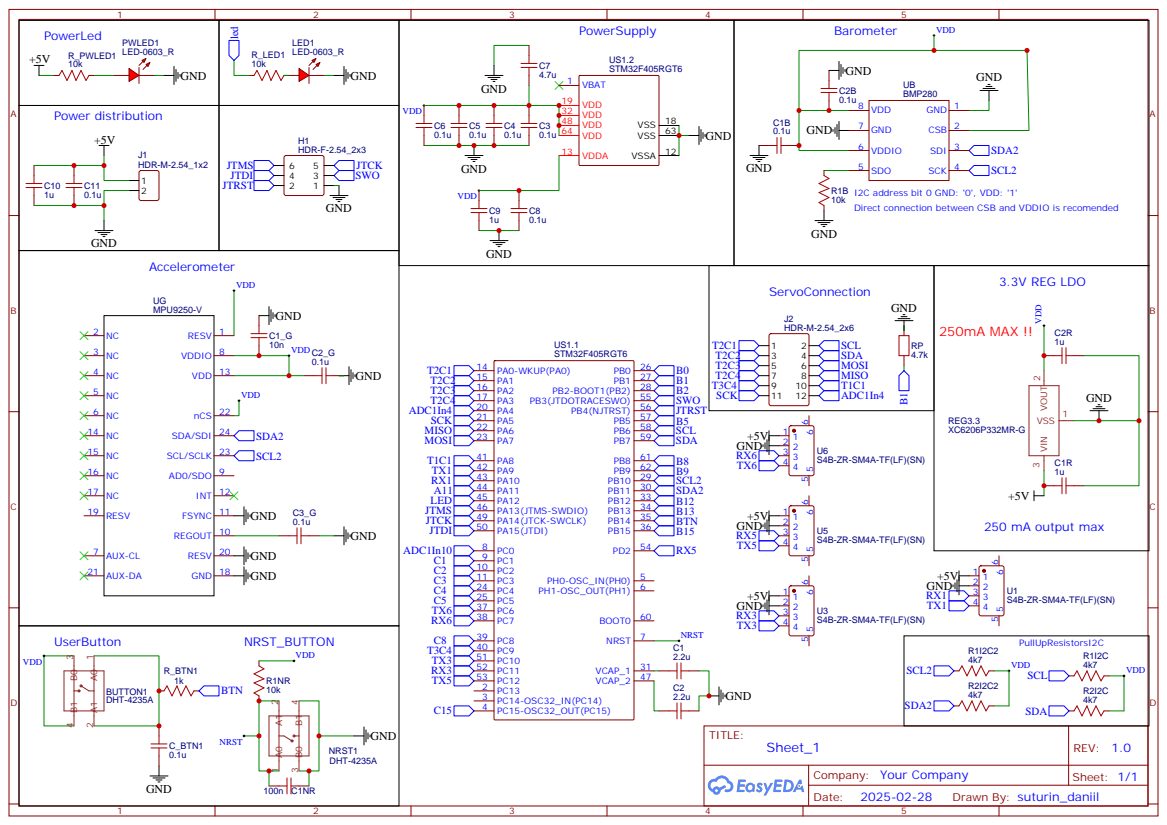
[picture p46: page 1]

I2C address bit 0 GND: '0', VDD: '1'
Direct connection between CSB and VDDIO is recomended

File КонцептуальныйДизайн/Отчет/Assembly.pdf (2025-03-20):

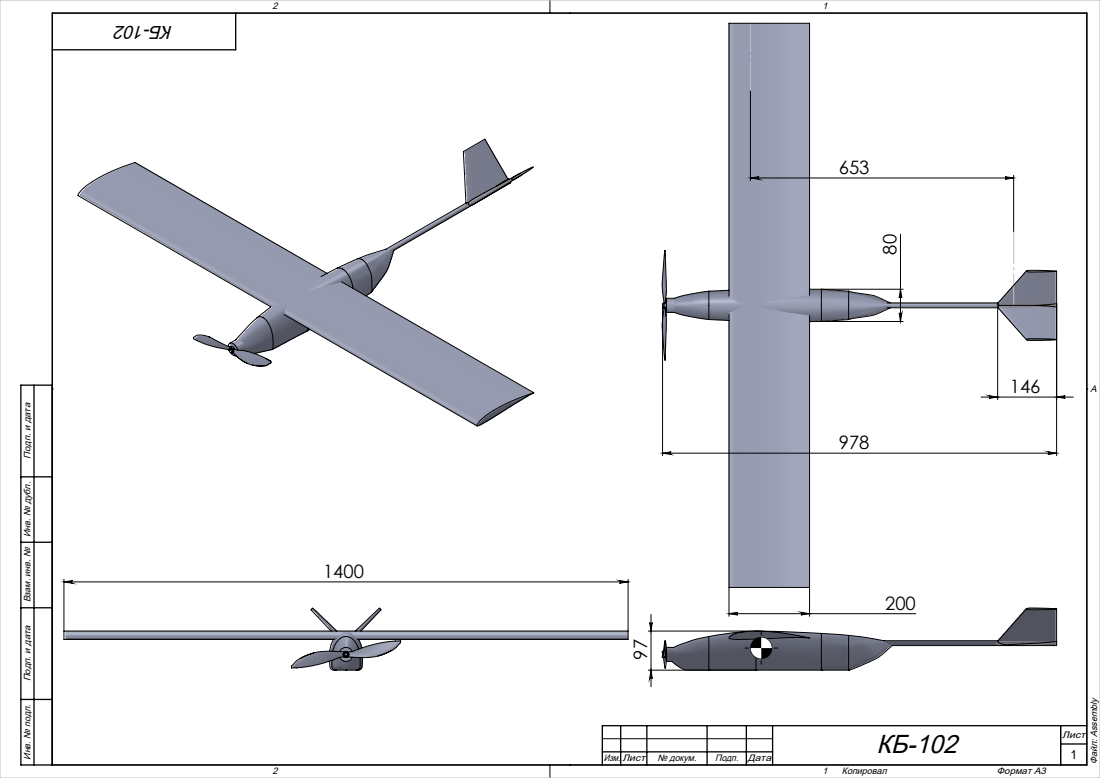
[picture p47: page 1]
Инв. № подл.; № докум.; Подп.; Дата; Формат А3; Файл: Assembly A

Подп. и дата Взам. инв. № Инв. № дубл. Подп. и дата

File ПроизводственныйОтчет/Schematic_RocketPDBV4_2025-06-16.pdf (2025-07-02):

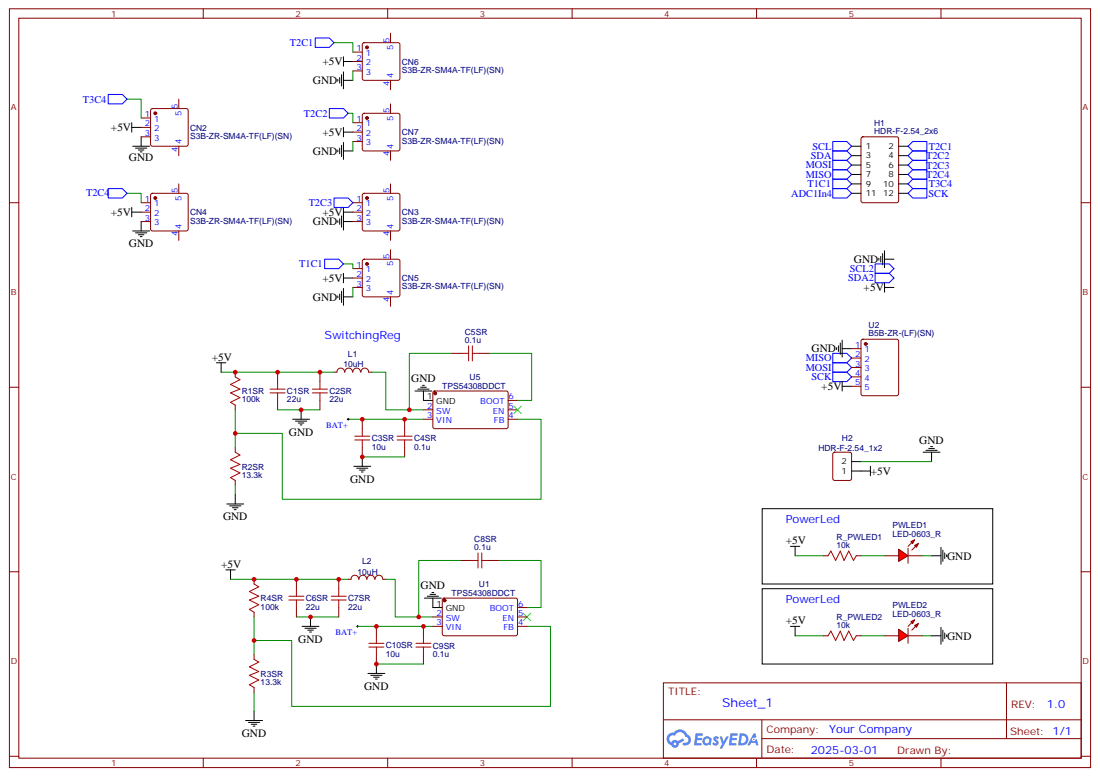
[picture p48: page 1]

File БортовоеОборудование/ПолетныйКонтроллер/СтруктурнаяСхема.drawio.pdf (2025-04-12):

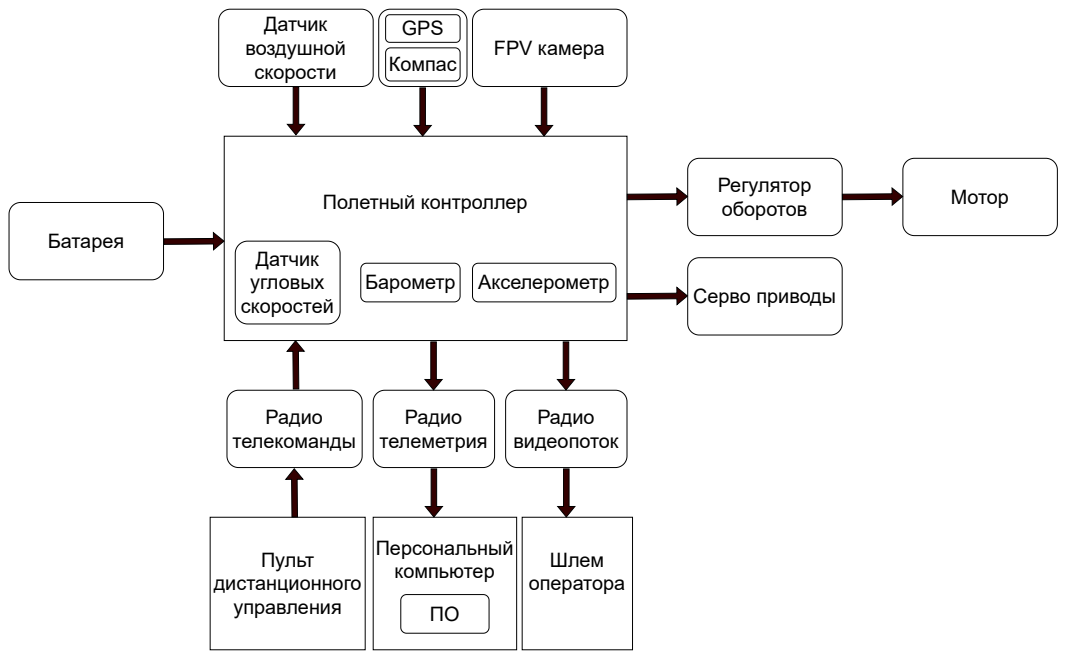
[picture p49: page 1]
Полетный контроллер; Датчик угловых скоростей; Барометр; Датчик воздушной скорости; GPS; Батарея; FPV камера; Радио телекоманды; Радио телеметрия; Регулятор оборотов; Мотор; Серво приводы; Радио видеопоток; Персональный компьютер; Шлем оператора; Пульт дистанционного управления; Компас; Акселерометр

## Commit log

2025-03-12 Добавил Readme файл
2025-03-12 Добавил папку концептуального дизайна
    [WeightData.xlsx]
2025-03-14 Добавил предварительный график работ
    [ГрафикРабот.xlsx]
2025-03-14 Обновил график
    [ГрафикРабот.xlsx]
2025-03-14 Перенес график работ в онлайн
2025-03-20 Добавил модель ЛА
    [Assembly.SLDASM, Assembly.SLDDRW, ConceptPlane.SLDPRT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]
2025-03-20 Добавил концепт
2025-03-20 Добавил отчет
2025-03-27 Добавил папку промежуточного дизайна
2025-03-27 Добавил смету
    [Смета.xlsx]
2025-03-29 Обновил данные по потребляемой мощности ВМГ
2025-03-30 Добавил схему соединений и характеристики датчиков
2025-03-30 Добавил папку модели ЛА
    [ESC.SLDPRT, FCBoard1.SLDPRT, FCBoard2.SLDPRT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]
2025-03-30 Добавил таблицу потребляемой мощности
2025-03-30 Добавил папку бортового оборудования
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2025-03-30 Полетный контроллер Изменил названия файлов
2025-03-30 Положил папку ПК в БО
2025-04-06 Дин. модель: поступательное движение
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2025-04-12 Обновил структурную схему и схему соединений
2025-04-12 Упрощенный ветер + параметры в скрипте
2025-04-13 Поправил характеристки используемого БО
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2025-04-13 Новые модели компонентов
    [2p4s18650.SLDASM, AileronL.SLDPRT, AileronR.SLDPRT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]
2025-04-13 Новые позиции
    [Смета.xlsx]
2025-04-13 Добавил папку аэродинамики
    [LiftCurveSlope.csv, SD7032 C_L.csv, xf-n0009sm-il-500000.csv]
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2025-04-14 Добавил в ноутбук расчетные формулы
2025-04-15 Добавил новые методы класса UAV
2025-04-15 Новая модель крыла
    [AileronL.SLDPRT, AileronR.SLDPRT, Assembly.SLDASM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]
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2025-04-17 Добавил функцию расчета коэфф лоб сопр
2025-04-17 Добавил учет хвостового оперения
2025-04-19 Функция для подсчета минимального оспротивления ЛА готова
2025-04-20 Добавил учет управляющих поверхностей
    [AirfoilFlapCoeff02.csv, AirfoilFlapCoeff025.csv, AirfoilFlapCoeff03.csv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]
2025-04-20 Добавил построение балансировочной кривой
2025-04-21 Добавил отрисовку центра давления
    [ComponentsMass.xlsx, SD7032 C_L.csv, xf-n0009sm-il-500000.csv]
2025-04-21 Добавил в отчет расчеты из ноутбука
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2025-04-27 Кин. ур. Эйлера и прочие улучшения
2025-04-27 Добавил модель пропеллера и добавил константы мотора в файл с параметриами
2025-04-27 Исправил подсчет момента мотора через векторное произведение
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2025-04-28 Добавил в отчет БО и СУ
2025-04-29 Дополнил отчет дин моделью и центровочной ведомойстью
2025-04-30 Добавил комментарии в код и добавил функцию V-n диаграммы
    [AirfoilFlapCoeff02.csv, AirfoilFlapCoeff025.csv, AirfoilFlapCoeff03.csv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]
2025-04-30 Добавил проектный отчет
    [AirfoilFlapCoeff02.csv, AirfoilFlapCoeff025.csv, AirfoilFlapCoeff03.csv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]
2025-04-30 Добавил в список батареи
    [Смета.xlsx]
2025-05-04 Исправил ошибки в подсчете коэфф лобового оспротивления
2025-05-04 Ссылка на приращение коэфф лобового сопротивления за счет отклонения рулей
2025-05-04 Добавил код для масштабирования, поворота и смещения координат профилей
2025-05-06 Добавил возможнось бобавлять координату z профиля
    [AssemblyNew.SLDASM, tracker_v2024.step, tracker_v2025.step]
2025-05-11 Начал разработку 3Д модели по уточненным аэродинамическим расчетам
    [2p4s18650.SLDASM, Fuselage.SLDPRT, JXServo.SLDPRT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]
2025-05-11 Добавил файл размеров, лежит в корне, т.к. солид не видит файлы с путем, содержащий кириллицу
2025-05-14 Добавил модель крыла. Правое крыло копирует левое, изменяя геометрию левого, правое меняется автоматически, но не наоборот
    [КрылоЛевое.SLDPRT]
2025-05-14 Правое крыло
    [КрылоПравое.SLDPRT]
2025-05-14 Элероны изменяются так же как и крыло, изменяя левый элерон, правый меняется автоматически
    [ЭлеронЛевый.SLDPRT, ЭлеронПравый.SLDPRT]
2025-05-14 Вместо кучи трубок разного диаметра оставил одну, завязав на файл с уравнениями, где переменная DFusTube отвечает за диаметр трубки фюзеляжа
    [ОсновнаяТрубкаФюзеляжа.SLDPRT]
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2025-05-14 Прошлый файл с уравнениями оказался пустым, сейчас исправил, добавив несколько новых переменных: САХ, размах
2025-05-14 Добавил в сборку крыло и элероны
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2025-05-14 Убрал лишние файлы
    [Fuselage.SLDPRT, УгольнаяТрубка10х8х1000мм.SLDPRT, УгольнаяТрубка12х10х1000мм.SLDPRT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]
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2025-06-30 Добавил актуальную сборку в версии SW2021
    [2p4s18650.SLDASM, 3DPrintedTail.SLDPRT, Assembly.SLDDRW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]
2025-06-30 Добавил STEP модель сборки
2025-06-30 Удалили старые файлы'
    [Assembly.SLDDRW, Fuselage.SLDPRT]
2025-06-30 Добавил файл с продувкой модели
    [CFD_Result.xlsx]
2025-07-02 Добавил новую смету
    [Смета.xlsx]
2025-07-02 Добавил новый файл для модели, содержащий только глобальные переменные без уравнений, так удобнее
2025-07-02 Обновил модель
    [3DPrintedTail.SLDPRT, 3DPrintedTailGrid.STL, 3DPrintedTailSurf.STL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]
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2025-07-02 Доп файлы для производственного отчета
    [CFD_Result.xlsx]
2025-07-02 Добавил файлы трассировки платы
    [PCB_RocketBoardV4_2025-05-21.pcbdoc, PCB_RocketPDBV4_2025-05-21.pcbdoc]
2025-07-02 Добавил папку производственного отчета
2025-07-06 Добавил папку с нашим ПК
    [PCB_RocketBoardV4_2025-05-21.pcbdoc, PCB_RocketPDBV4_2025-05-21.pcbdoc]
2025-07-06 Обновил STEP файл сборки
2025-07-06 Обновил сборку
    [3DPrintedElevatorR.SLDPRT, 3DPrintedTail.SLDPRT, 3DPrintedTailGrid.STL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]
2025-07-06 Перенес проект платы в папку с нашим ПК
    [PCB_RocketBoardV4_2025-05-21.pcbdoc, PCB_RocketPDBV4_2025-05-21.pcbdoc]
